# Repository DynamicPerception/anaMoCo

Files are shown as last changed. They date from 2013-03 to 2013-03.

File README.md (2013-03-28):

anaMoCo Board
=============

The anaMoCo board is the heart of the [AT<sup>2</sup> two-axis analog controller](http://dynamicperception.com/products/at2-motion-controller)
 sold by Dynamic Perception.

This controller supports control of two DC motors from 6-16V at up to 1.2A each axis.

Key Features
------------

- Control up to two DC motor axes
     - 6-16V power input/output
     - Up to 1.2A per axis
- 99% Analog (one final PWM stage)
     - No microcontroller
- Support for input from a two axis, pot-style joystick and two knobs
- Analog damping support
- Cruise control
- Direction inversion
- Locking DC Jacks

License and Copyright
---------------------

anaMoCo and the AT<sup>2</sup> are Copyright (c) 2012-2013 Dynamic Perception LLC.

All files shared under the Creative Commons Attibution-Share-Alike 3.0 License.

anaMoCo and AT<sup>2</sup> names are trademarks of Dynamic Perception LLC.

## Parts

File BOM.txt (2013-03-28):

Partlist

Exported from joystick_motor_controller.sch at 11/20/2012 9:31:51 AM

EAGLE Version 6.2.0 Copyright (c) 1988-2012 CadSoft

Assembly variant: 

Part     Value              Device                 Package           Library             Sheet

C1       .01uF              CAP_NONPOL0402         0402_CAP          parkers_parts       1
C2       .1uF               CAP_NONPOL0402         0402_CAP          parkers_parts       1
C3       100uF              CAP_POLARIZED6.3MM_SMD 6.3MM_DIA_CAP_SMD parkers_parts       1
C4       .01uF              CAP_NONPOL0402         0402_CAP          parkers_parts       1
C5       .1uF               CAP_NONPOL0402         0402_CAP          parkers_parts       1
C6       .1uF               CAP_NONPOL0402         0402_CAP          parkers_parts       1
C7       .1uF               CAP_NONPOL0402         0402_CAP          parkers_parts       1
C8       .1uF               CAP_NONPOL0402         0402_CAP          parkers_parts       1
C9       100uF              CAP1206                1206              SparkFun-Passives   1
C10      100uF              CAP1206                1206              SparkFun-Passives   1
C11      100uF              CAP1206                1206              SparkFun-Passives   1
C12      100uF              CAP1206                1206              SparkFun-Passives   1
D1       CSFMT108-HF        1N4148WSOD-123         SOD-123           parkers_parts       1
D2       CSFMT108-HF        1N4148WSOD-123         SOD-123           parkers_parts       1
D3       CSFMT108-HF        1N4148WSOD-123         SOD-123           parkers_parts       1
D4       CSFMT108-HF        1N4148WSOD-123         SOD-123           parkers_parts       1
D5       CSFMT108-HF        1N4148WSOD-123         SOD-123           parkers_parts       1
D6       CSFMT108-HF        1N4148WSOD-123         SOD-123           parkers_parts       1
D7       CSFMT108-HF        1N4148WSOD-123         SOD-123           parkers_parts       1
D8       CSFMT108-HF        1N4148WSOD-123         SOD-123           parkers_parts       1
J1       JOYSTICK_1         M03POLAR               MOLEX-1X3         SparkFun-Connectors 1
J2       JOYSTICK_2         M03POLAR               MOLEX-1X3         SparkFun-Connectors 1
J3       MOTOR_PWR          POWER_JACKPTH          POWER_JACK_PTH    SparkFun-Connectors 1
J4       M2_OUTPUT          POWER_JACKPTH          POWER_JACK_PTH    SparkFun-Connectors 1
J5       M1_OUTPUT          POWER_JACKPTH          POWER_JACK_PTH    SparkFun-Connectors 1
P1       EVU-F3MFL3B53      POTENTIOMETERPTV09A-4  PTV09A-4_POT      parkers_parts       1
P2       EVU-F3MFL3B53      POTENTIOMETERPTV09A-4  PTV09A-4_POT      parkers_parts       1
R1       100K               RESISTOR0402           0402_RES          parkers_parts       1
R2       470K               RESISTOR0402           0402_RES          parkers_parts       1
R3       1M                 RESISTOR0402           0402_RES          parkers_parts       1
R4       6.04K              RESISTOR0402           0402_RES          parkers_parts       1
R5       2.1K               RESISTOR0402           0402_RES          parkers_parts       1
R6       6.04K              RESISTOR0402           0402_RES          parkers_parts       1
R7       220                RESISTOR0402           0402_RES          parkers_parts       1
R8       220                RESISTOR0402           0402_RES          parkers_parts       1
R9       5.36K              RESISTOR0402           0402_RES          parkers_parts       1
R10      4.7K               RESISTOR0402           0402_RES          parkers_parts       1
R11      6.04K              RESISTOR0402           0402_RES          parkers_parts       1
R12      2.1K               RESISTOR0402           0402_RES          parkers_parts       1
R13      6.04K              RESISTOR0402           0402_RES          parkers_parts       1
R14      4.7K               RESISTOR0402           0402_RES          parkers_parts       1
R15      5.36K              RESISTOR0402           0402_RES          parkers_parts       1
R16      100K               RESISTOR0402           0402_RES          parkers_parts       1
R17      470K               RESISTOR0402           0402_RES          parkers_parts       1
R18      1M                 RESISTOR0402           0402_RES          parkers_parts       1
SW1      SPPH410100         PS004_SWPS004          PS004_SW          parkers_parts       1
SW2      0S202011MA0QN1     DPDTOS202011MA0QN1     OS202011MA0QN1    parkers_parts       1
SW3      SPPH410100         PS004_SWPS004          PS004_SW          parkers_parts       1
SW4      0S202011MA0QN1     DPDTOS202011MA0QN1     OS202011MA0QN1    parkers_parts       1
U1       LM324NSRE4         LM324SOP-14            SOP-14            parkers_parts       1
U2       LM324NSRE4         LM324SOP-14            SOP-14            parkers_parts       1
U3       L298_BRIDGE_DRIVER L298_BRIDGE_DRIVER     POWERSO20         SparkFun-PowerIC    1
U4       TS2937CW50         V_REG_MIC2920          SOT223            SparkFun-PowerIC    1
U5       TS3A5018           TS3A5018TTSOP-16       TTSOP-16          parkers_parts       1
U6       TS3A5018           TS3A5018TTSOP-16       TTSOP-16          parkers_parts       1

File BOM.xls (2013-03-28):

Partlist
Board | anaMoCo
REV | 7
Part Sheet | Value | Part Number | Notes
C1 | 0.01uF | TMK105B7103KV-F
C2 | 0.1uF | GRM155R61E104KA7D
C3 | 100uF | UWZ1V101MCL1GS
C4 | 0.01uF | TMK105B7103KV-F
C5 | 0.1uF | GRM155R61E104KA7D
C6 | 0.1uF | GRM155R61E104KA7D
C7 | 0.1uF | GRM155R61E104KA7D
C8 | 0.1uF | GRM155R61E104KA7D
C9 | 100uF | GRM31CF50J107ZE01L
C10 | 100uF | GRM31CF50J107ZE01L
C11 | 100uF | GRM31CF50J107ZE01L
C12 | 100uF | GRM31CF50J107ZE01L
D1 |  | PMEG3010EH,115
D2 |  | PMEG3010EH,115
D3 |  | PMEG3010EH,115
D4 |  | PMEG3010EH,115
D5 |  | PMEG3010EH,115
D6 |  | PMEG3010EH,115
D7 |  | PMEG3010EH,115
D8 |  | PMEG3010EH,115
MOTOR_PWR |  | KLDX-0202-A-LT | 2.1mm Locking DC Jack
M1_OUTPUT |  | KLDX-0202-B-LT | 2.5mm Locking DC Jack
M2_OUTPUT |  | KLDX-0202-B-LT | 2.5mm Locking DC Jack
P1 | 5K | EVU-F3MFL3B53 | Knob for Pot: 450-4763
P2 | 5K | EVU-F3MFL3B53 | Knob for Pot: 450-4763
R1 | 100K | WR04X1003FTL
R2 | 470K | CR0402-FX-4703GLF
R3 | 1M | 304-1.0M-RC
R4 | 6.04K | 304-6.04K-RC
R5 | 2.1K | 304-2.1K-RC
R6 | 6.04K | 304-6.04K-RC
R7 | 220 | CRCW0402220RFKED | DO NOT POPULATE
R8 | 220 | CRCW0402220RFKED | DO NOT POPULATE
R9 | 5.36K | 304-5.36K-RC
R10 | 4.7K | CR0402-FX-4701GLF
R11 | 6.04K | 304-6.04K-RC
R12 | 2.1K | 304-2.1K-RC
R13 | 6.04K | 304-6.04K-RC
R14 | 4.7K | CR0402-FX-4701GLF
R15 | 5.36K | 304-5.36K-RC
R16 | 100K | WR04X1003FTL
R17 | 470K | CR0402-FX-4703GLF
R18 | 1M | 304-1.0M-RC
SW1 |  | SPPH410100 | Cap for SW: PV BK
SW2 |  | 0S202011MA0QN1
SW3 |  | SPPH410100 | Cap for SW: PV BK
SW4 |  | 0S202011MA0QN1
U1 |  | LM324NSRE4
U2 |  | LM324NSRE4
U3 |  | L298P013TR
U4 |  | TS2937CW50
U5 |  | TS3A5018
U6 |  | TS3A5018

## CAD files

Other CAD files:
SketchUP/Joystick.skp
SketchUP/Joystick_scaled.skp
SketchUP/main_board.skp
SketchUP/main_board_scaled.skp

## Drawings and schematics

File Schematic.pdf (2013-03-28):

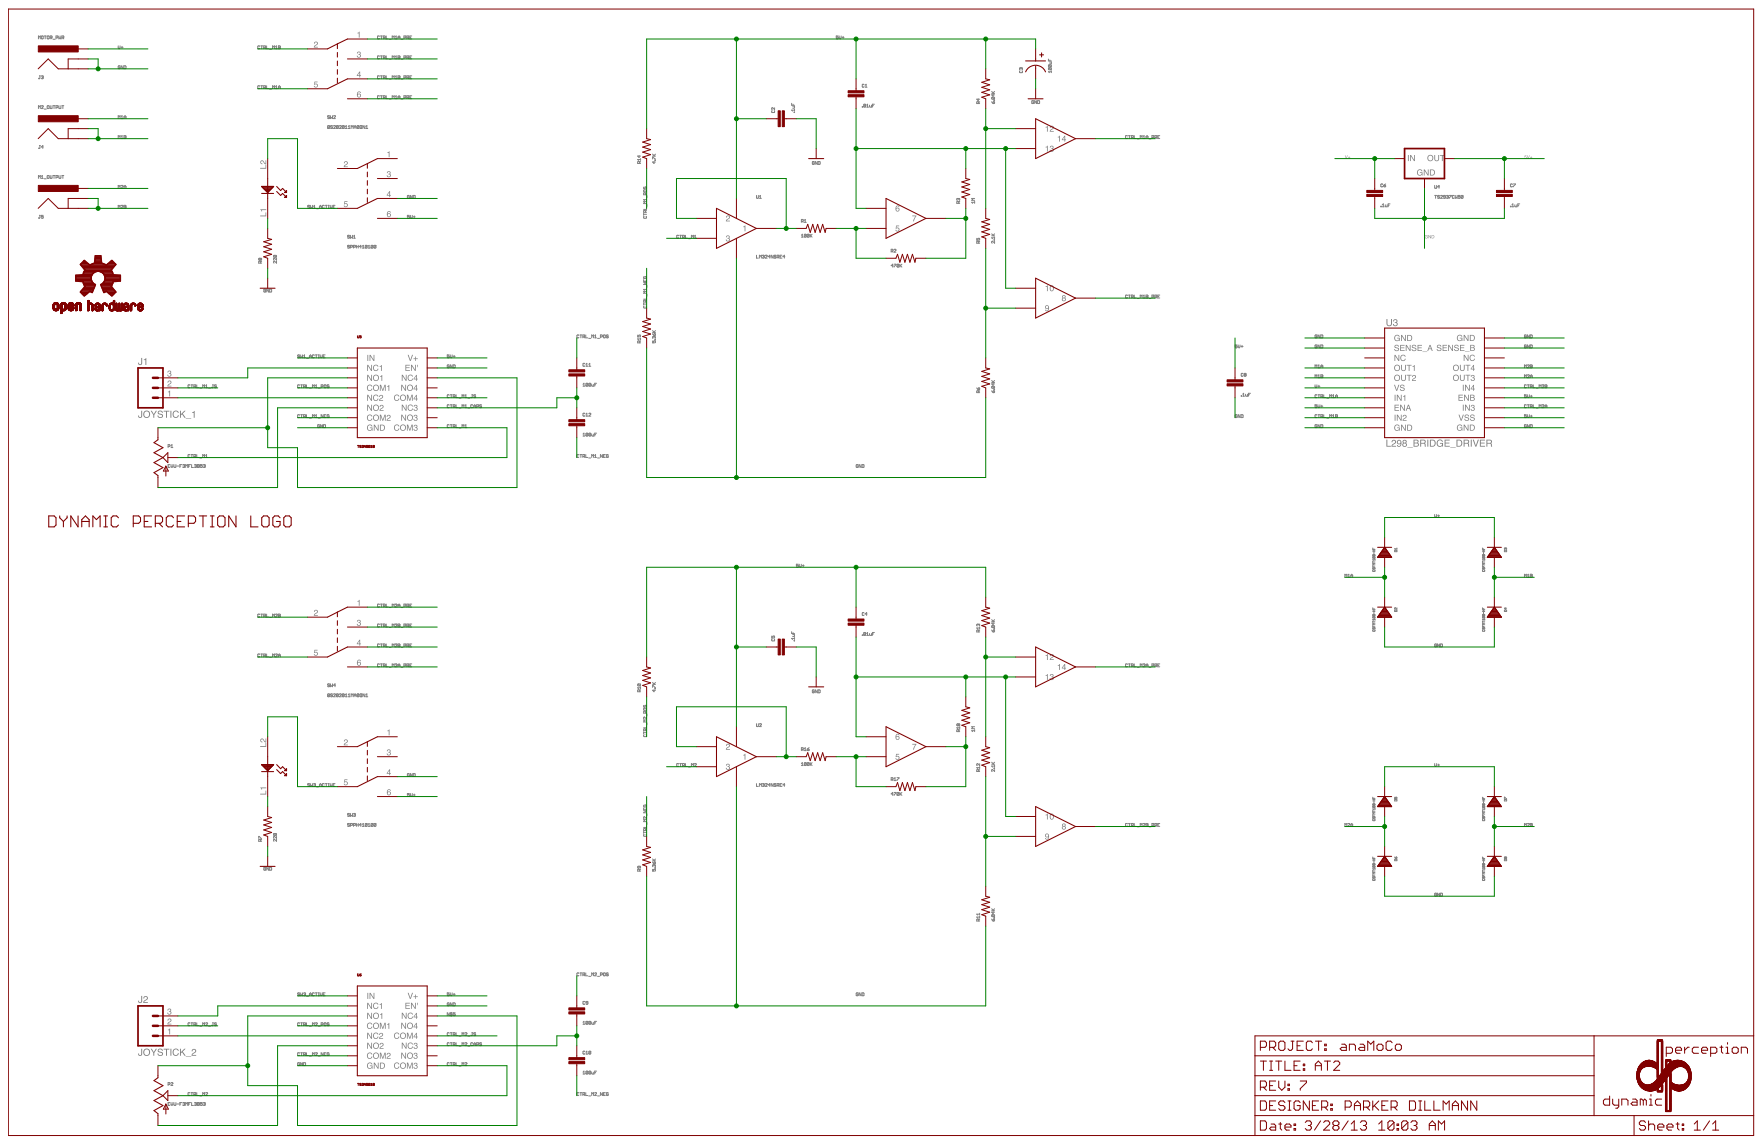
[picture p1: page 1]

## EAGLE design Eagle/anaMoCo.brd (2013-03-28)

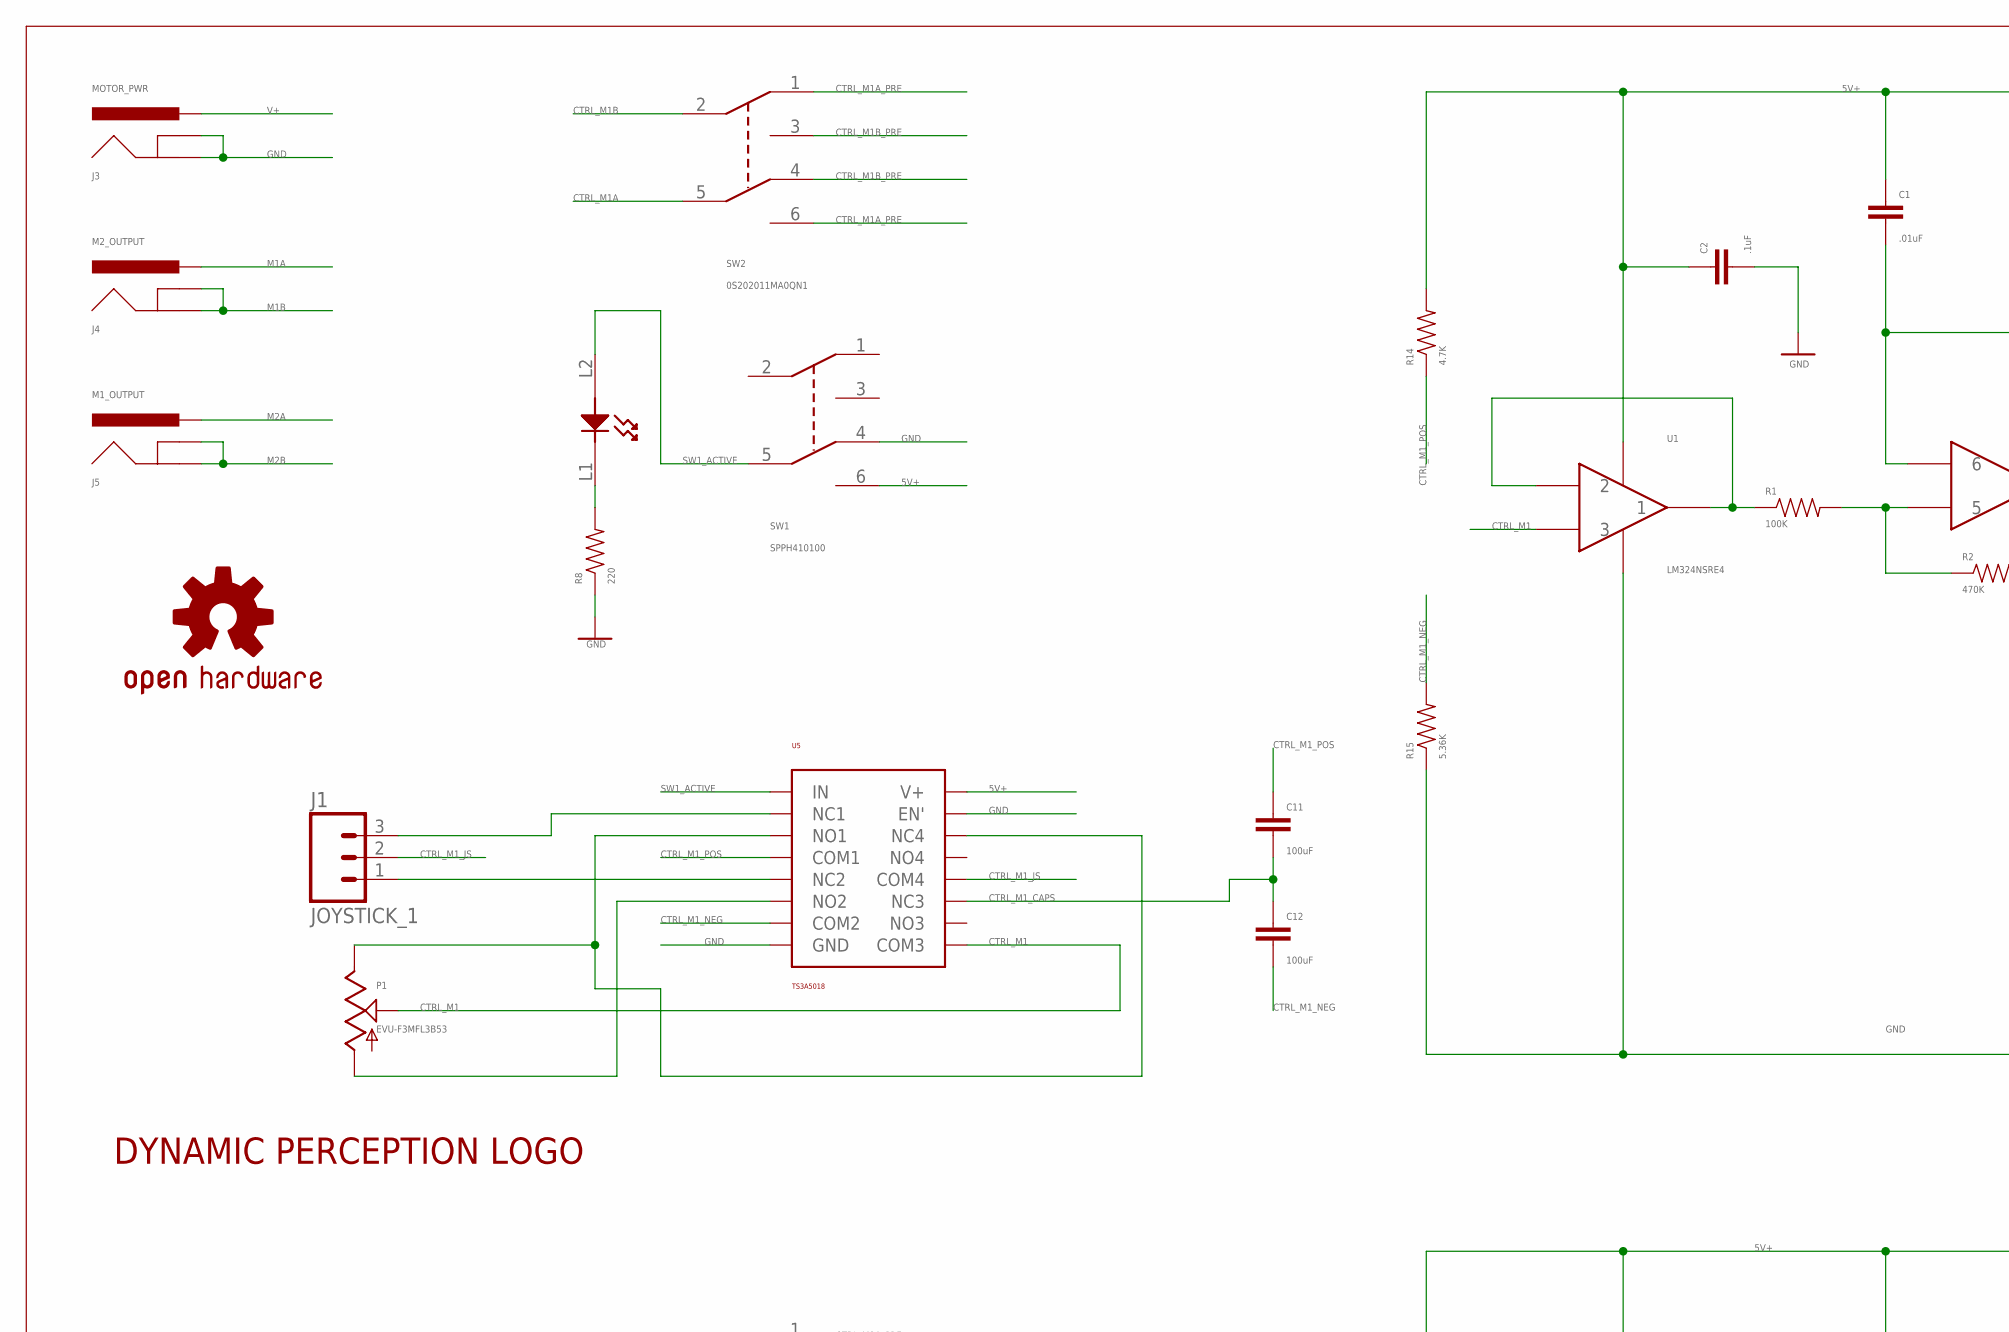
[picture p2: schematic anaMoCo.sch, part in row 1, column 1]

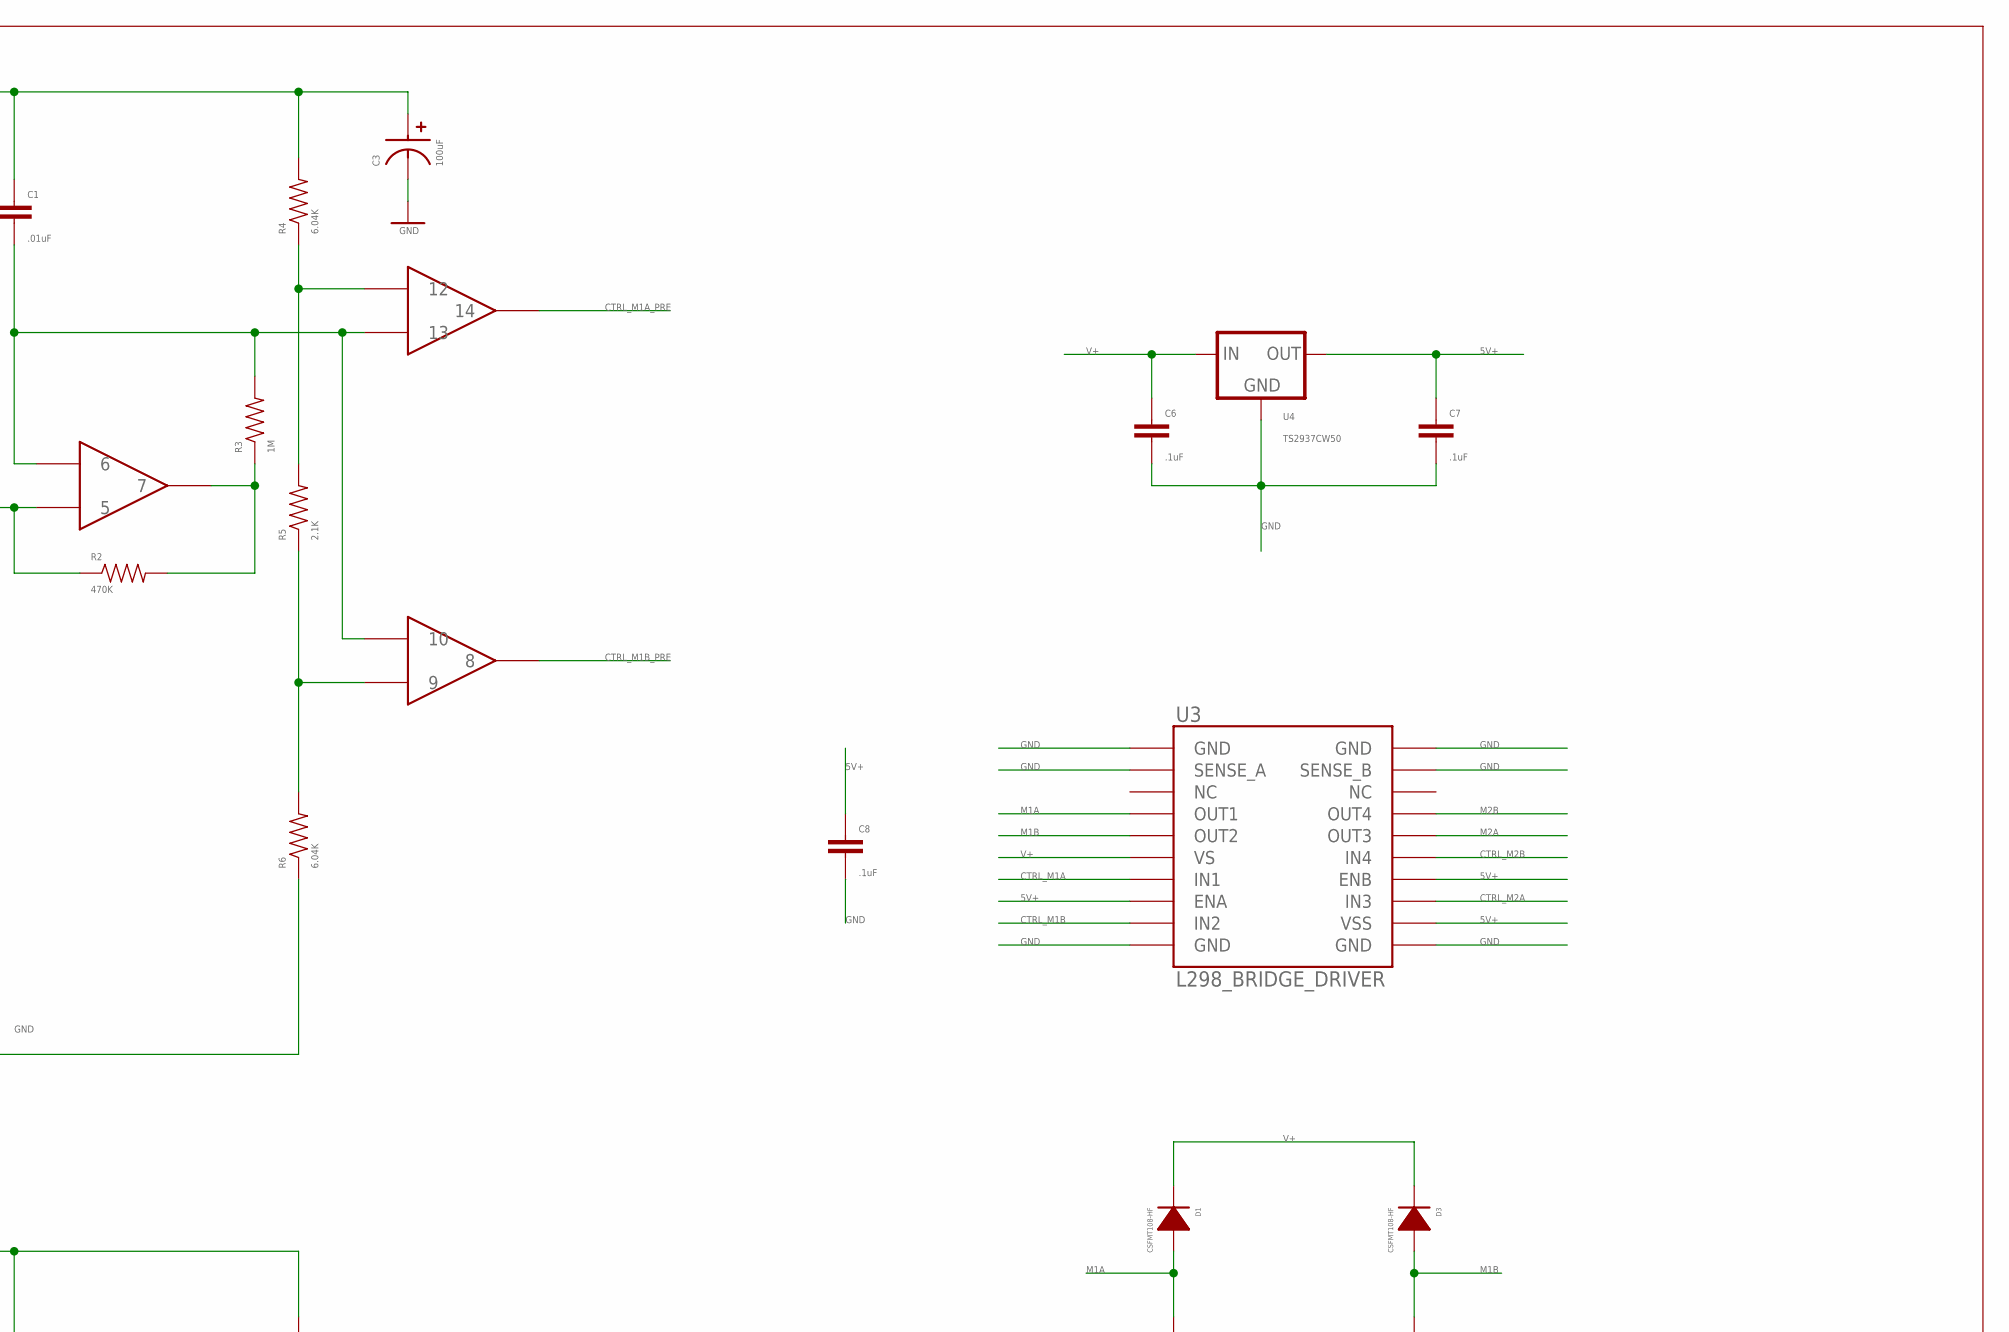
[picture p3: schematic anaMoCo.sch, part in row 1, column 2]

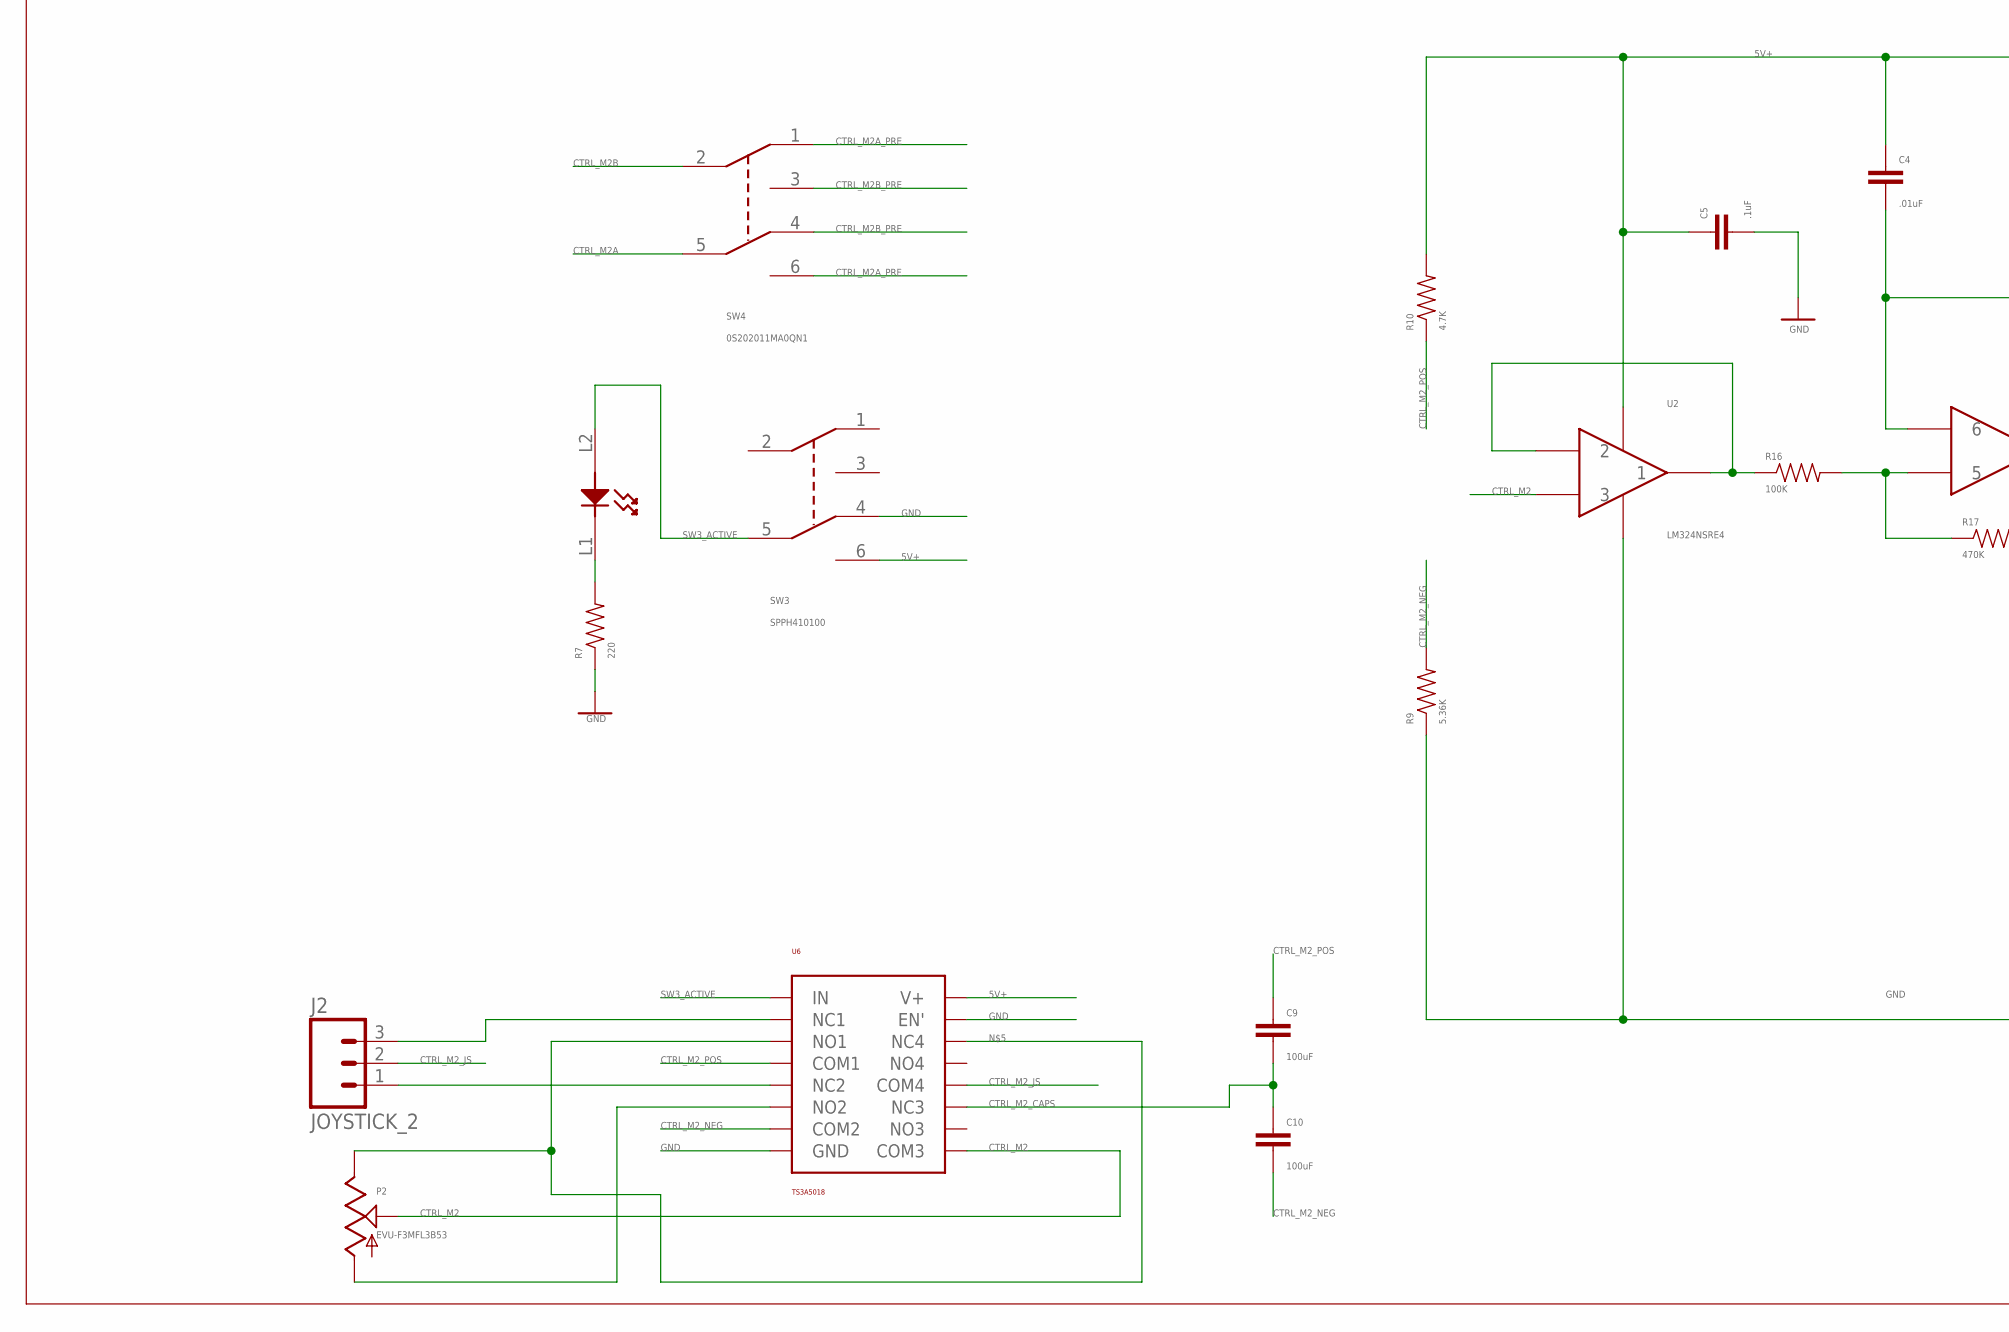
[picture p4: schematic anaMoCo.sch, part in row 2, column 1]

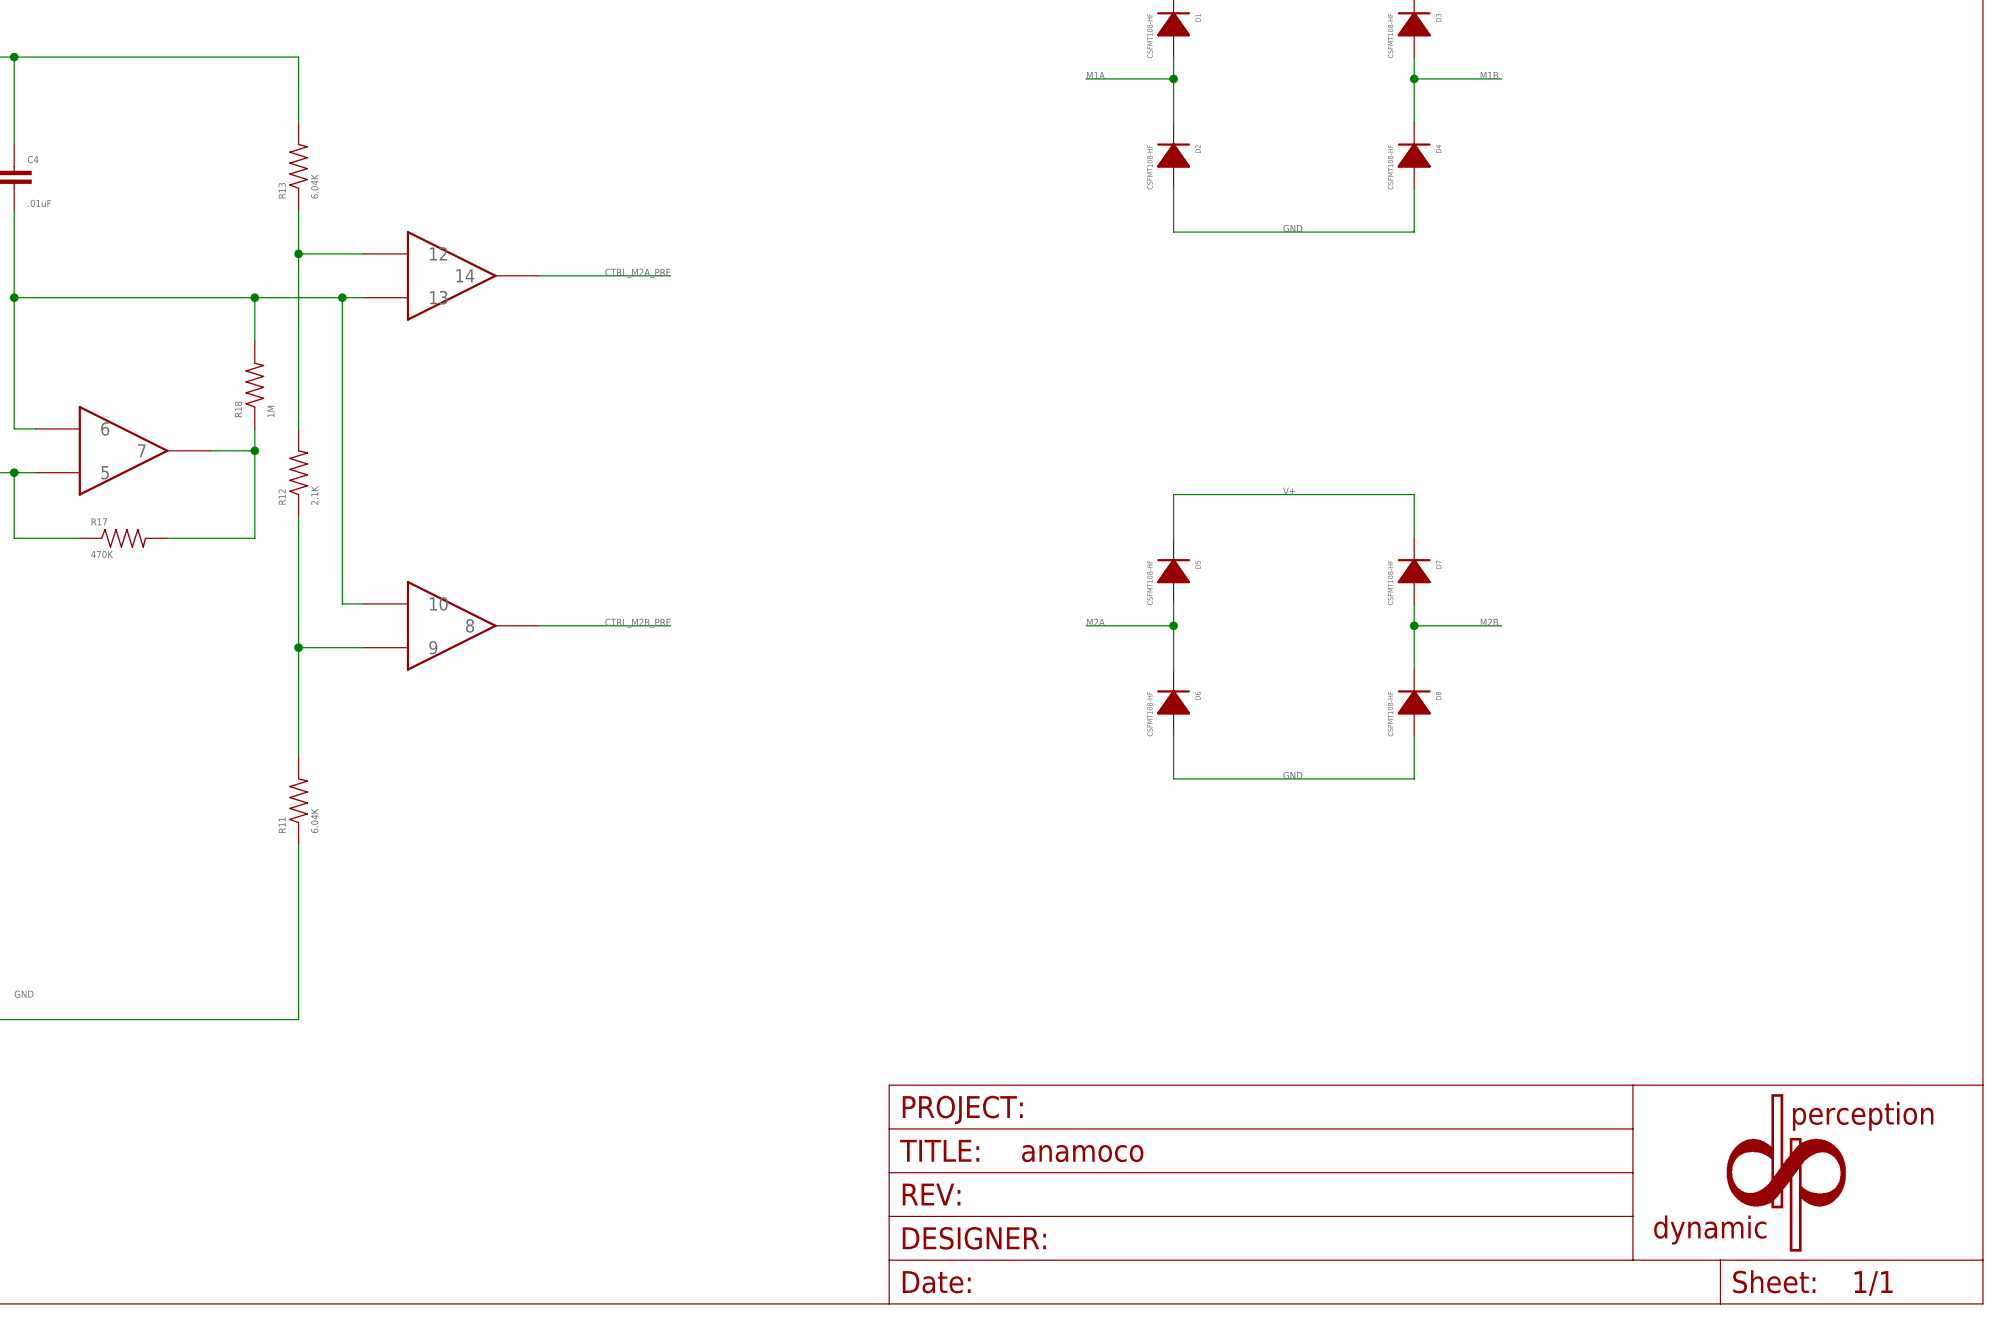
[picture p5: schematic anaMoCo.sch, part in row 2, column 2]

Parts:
C1, C4: .01uF; 0402_CAP
C2, C5, C6, C7, C8: .1uF; 0402_CAP
C3: 100uF; 6.3MM_DIA_CAP_SMD
C9, C10, C11, C12: 100uF; 1206
D1, D2, D3, D4, D5, D6, D7, D8: CSFMT108-HF; SOD-123
J1: JOYSTICK_1; MOLEX-1X3
J2: JOYSTICK_2; MOLEX-1X3
J3: MOTOR_PWR; POWER_JACK_PTH
J4: M2_OUTPUT; POWER_JACK_PTH
J5: M1_OUTPUT; POWER_JACK_PTH
LOGO1: DP_LOGOLARGE; DP_LOGO_LARGE
P1, P2: EVU-F3MFL3B53; PTV09A-4_POT
R1, R16: 100K; 0402_RES
R2, R17: 470K; 0402_RES
R3, R18: 1M; 0402_RES
R4, R6, R11, R13: 6.04K; 0402_RES
R5, R12: 2.1K; 0402_RES
R7, R8: 220; 0402_RES
R9, R15: 5.36K; 0402_RES
R10, R14: 4.7K; 0402_RES
SW1, SW3: SPPH410100; PS004_SW
SW2, SW4: 0S202011MA0QN1; OS202011MA0QN1
U1, U2: LM324NSRE4; SOP-14
U3: L298_BRIDGE_DRIVER; POWERSO20
U4: TS2937CW50; SOT223
U5, U6: TS3A5018; TTSOP-16
U$1: OSHW-LOGOM; OSHW-LOGO-M
U$2: DP_FRAME

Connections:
5V+: C1.1, C2.1, C3.POS, C4.1, C5.1, C7.1, C8.1, R4.2, R10.2, R13.2, R14.2, SW1.6, SW3.6, U1.4, U2.4, U3.8 (ENA), U3.12 (VSS), U3.14 (ENB), U4.3 (OUT), U5.16 (V+), U6.16 (V+)
BIAS2: R5.1, R6.2, U1.9
BIAS4: R11.2, R12.1, U2.9
BLAH: R4.1, R5.2, U1.12
BLAH2: R12.2, R13.1, U2.12
CTRL_M1: P1.2, U1.3, U5.9 (COM3)
CTRL_M1A: SW2.5, U3.7 (IN1)
CTRL_M1A_PRE: SW2.1, SW2.6, U1.14
CTRL_M1B: SW2.2, U3.9 (IN2)
CTRL_M1B_PRE: SW2.3, SW2.4, U1.8
CTRL_M1_CAPS: C11.2, C12.1, U5.11 (NC3)
CTRL_M1_JS: J1.2, U5.12 (COM4)
CTRL_M1_NEG: C12.2, R15.2, U5.7 (COM2)
CTRL_M1_POS: C11.1, R14.1, U5.4 (COM1)
CTRL_M2: P2.2, U2.3, U6.9 (COM3)
CTRL_M2A: SW4.5, U3.13 (IN3)
CTRL_M2A_PRE: SW4.1, SW4.6, U2.14
CTRL_M2B: SW4.2, U3.15 (IN4)
CTRL_M2B_PRE: SW4.3, SW4.4, U2.8
CTRL_M2_CAPS: C9.2, C10.1, U6.11 (NC3)
CTRL_M2_JS: J2.2, U6.12 (COM4)
CTRL_M2_NEG: C10.2, R9.2, U6.7 (COM2)
CTRL_M2_POS: C9.1, R10.1, U6.4 (COM1)
GND: C2.2, C3.NEG, C5.2, C6.2, C7.2, C8.2, D2.ANODE, D4.ANODE, D6.ANODE, D8.ANODE, J3.GND, J3.GNDBREAK, R6.1, R7.1, R8.1, R9.1, R11.1, R15.1, SW1.4, SW3.4, U1.11, U2.11, U3.1 (GND), U3.2 (SENSE_A), U3.10 (GND), U3.11 (GND), U3.19 (SENSE_B), U3.20 (GND), U4.2 (GND), U5.8 (GND), U5.15 (EN'), U6.8 (GND), U6.15 (EN')
M1A: D1.ANODE, D2.CATHODE, J4.PWR, U3.4 (OUT1)
M1B: D3.ANODE, D4.CATHODE, J4.GND, J4.GNDBREAK, U3.5 (OUT2)
M2A: D5.ANODE, D6.CATHODE, J5.PWR, U3.16 (OUT3)
M2B: D7.ANODE, D8.CATHODE, J5.GND, J5.GNDBREAK, U3.17 (OUT4)
unnamed: R1.1, U1.1, U1.2
unnamed: R1.2, R2.1, U1.5
unnamed: R2.2, R3.1, U1.7
unnamed: C1.2, R3.2, U1.6, U1.10, U1.13
unnamed: P2.1, U6.3 (NO1), U6.14 (NC4)
unnamed: P2.3, U6.6 (NO2)
unnamed: R8.2, SW1.L1 (L2)
unnamed: P1.1, U5.3 (NO1), U5.14 (NC4)
unnamed: R7.2, SW3.L1 (L2)
unnamed: J2.3, U6.2 (NC1)
unnamed: J2.1, U6.5 (NC2)
unnamed: J1.3, U5.2 (NC1)
unnamed: J1.1, U5.5 (NC2)
unnamed: R16.1, U2.1, U2.2
unnamed: R16.2, R17.1, U2.5
unnamed: R17.2, R18.1, U2.7
unnamed: C4.2, R18.2, U2.6, U2.10, U2.13
unnamed: P1.3, U5.6 (NO2)
SW1_ACTIVE: SW1.5, SW1.L2 (L1), U5.1 (IN)
SW3_ACTIVE: SW3.5, SW3.L2 (L1), U6.1 (IN)
V+: C6.1, D1.CATHODE, D3.CATHODE, D5.CATHODE, D7.CATHODE, J3.PWR, U3.6 (VS), U4.1 (IN)

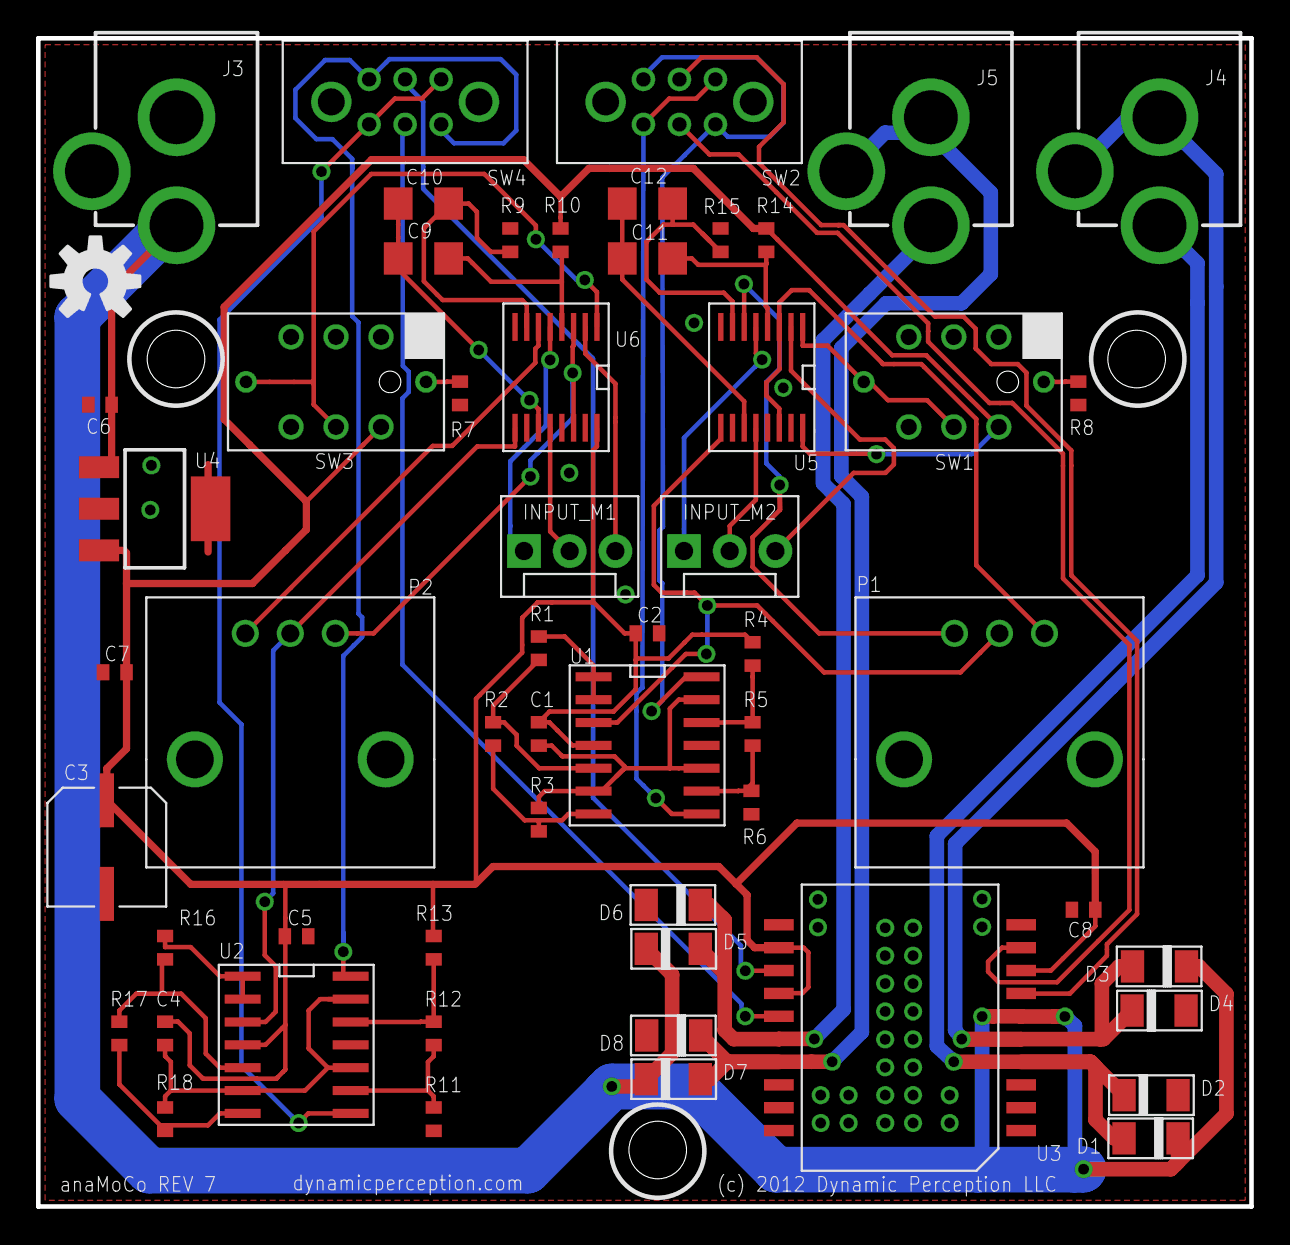
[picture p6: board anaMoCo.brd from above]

Board: 2 copper layers, 67.4 x 64.9 mm, 58 parts (1 on the bottom side), 49 nets.

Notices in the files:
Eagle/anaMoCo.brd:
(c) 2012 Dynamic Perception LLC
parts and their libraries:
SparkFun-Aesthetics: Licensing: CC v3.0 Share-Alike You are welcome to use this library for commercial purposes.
